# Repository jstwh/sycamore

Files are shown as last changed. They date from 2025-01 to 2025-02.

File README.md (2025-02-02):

# Sycamore

A python framework for Quad-EX.

### Contribution Guidelines

Branch names should state your name and purpose: e.g. joost/walking-engine

All files are formatted with the ruff formatter. Usage: ruff format

Make a branch, don't commit directly to main. If you want to, fork the repo.

### Setup

Create a venv, and install the dependencies as specified in `requirements.txt`:

```sh
python -m venv .venv
source .venv/bin/activate
pip install -r requirements.txt
```

### Setting Up Permissions

Run the following script to set up the necessary permissions for accessing input devices (controller):

```bash
./setup.sh
```

### Linux Service

There is a linux service that runs on startup, it is necessary to display the raspberry pi ip on the lcd, it executes: "python main.py --motors", so it does not turn on motors. The contents of the linux service file can be found in the sycamore.service file in the linux folder. The actual file is present on the raspberry pi under:

```
/etc/systemd/system/sycamore.service
```

some commands for usage:

```
sudo systemctl daemon-reload
sudo systemctl restart sycamore.service
sudo systemctl status sycamore.service

# Uses killsignal SIGINT which works like a keyboard interrupt
sudo systemctl stop sycamore.service
```

If the program fails (for example the ip doesn’t show up) the error gets redirected and can be seen with the command:

```
journalctl -u sycamore.service -f
```

### Arduino

The files for arduino can be found under the arduino map. The file "main.ino" is currently on the arduino and handles showing the ip and streaming data from the ultrasonic distance sensors from the arduino to the raspberry pi.

There is also an "imu.ino" file which was used to test the imu but is not integrated yet. It is up to future collaborators to properly integrate the imu. Note that the imu is currently also not properly placed within Quad-EX, this should also be done for it to work as intended.

For further information about the IMU, see [https://learn.adafruit.com/adafruit-bno055-absolute-orientation-sensor/arduino-code]().

### Argparse

Argparse is an argument parser for python and is used within sycamore to enable or disable certain features on execution. Note that the values are boolean and that the action thus determines the default and what it does. For example:

```
parser.add_argument(
        "--arduino",
        action="store_false",
    )
```

store_false means that the default is True and that you can disable arduino by adding a --arduino flag. Please DO NOT do --arduino False, this is not necessary and will not work.

### Walking Engine

The walking engine is based on various papers, codebases and our own tinkering. Some useful links are:

[https://www.researchgate.net/publication/332374021_Leg_Trajectory_Planning_for_Quadruped_Robots_with_High-Speed_Trot_Gait]()

[https://spotmicroai.readthedocs.io/en/latest/kinematic/#setup-our-3d-ouput]()

[https://www.researchgate.net/publication/322594373_Inverse_Kinematic_Analysis_of_a_Quadruped_Robot]()

[https://github.com/miguelasd688/4-legged-robot-model]()

For documentation about how the walking engine works please contact Makerspace staff and ask for the final report from Quad-EX.

Some important notes are:

The coordinate frame for the foot matrix is:

```
        """
        -x
            |
            |
            |    /  z
            |   /
            |  /
            | /
            |/____________  -y
        """
```

The inverse kinematics, providing the joint angles for the servo's, are calculated in ik.py. These joint angles are then given by providing the LegPoints matrix, containing the end effectors of all four feet, into the JointAngleProvider. The joint angle provider will then provide the angles which can be passed on into the ServoFactory class which will move the actuators. Note that the actuators have a calibration that makes them work, this is why there are servo_flip and servo_map methods in ServoFactory.

### Manual Servo Calibration

The servo's are manually calibrated. This is based on how the legs should move. This entire process is done manually and we never made a consice calibration method. This, again, is something a new contributor might work on. The test_servos.py file is available for some testing when you're calibrating.

### Visualizations

In order to visualize the robot we use rerun. It is a state of the art robotics visualization program and we highly recommend looking it up and reading through the documentation before use. When you want to visualize something you should add the ipv4 from your laptop into rr.connect_tcp("[your laptop ip]:9876"). Note that you should have a rerun window open when you run this, it won't open a window by itself. There is a visualization.py file, most of it is outdated but we kept it in since it might give new contributors some idea of how to visualize something.

### Controller

The controller is something we worked on but it is not properly integrated into the framework, see margriet/controller-input. We recommend going for the evdev approach over the pygame approach for lower overhead and utilizing the controller for simple things should not require much effort besides what we have already implemented.

### Sensors

The sensors that we properly wrote code for are the distance sensors and the lcd. There are also two camera's. We have conducted tests with camera's in an isolated environment but they are not integrated into the framework yet. It might be worthwhile for a new contributor to work on this.

### Mechanical

See [here](build_instructions/README.md).

### Electronics

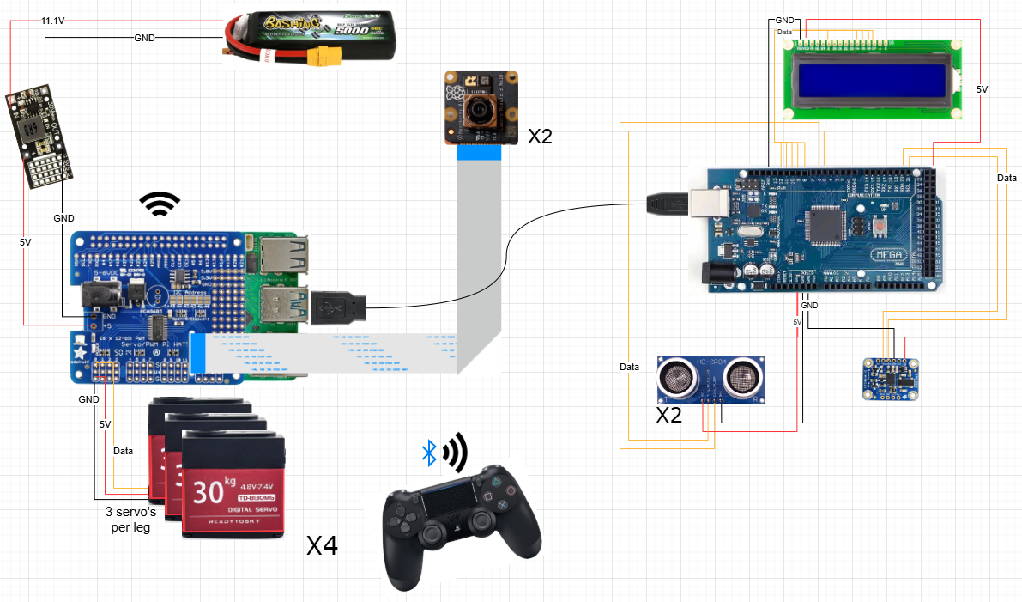
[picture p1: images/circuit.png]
Circuit


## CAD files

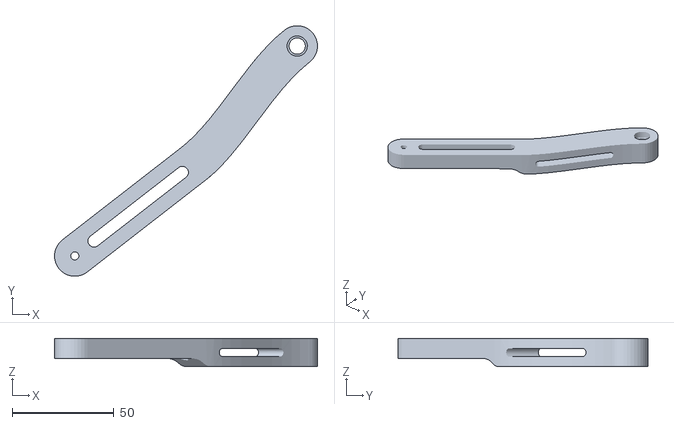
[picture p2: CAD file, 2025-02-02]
build_instructions/stl_files/Body_assemb - Leg_assembly_top_left-1 tibia_mirrored-1.STL
129.4 x 123.3 x 14.0

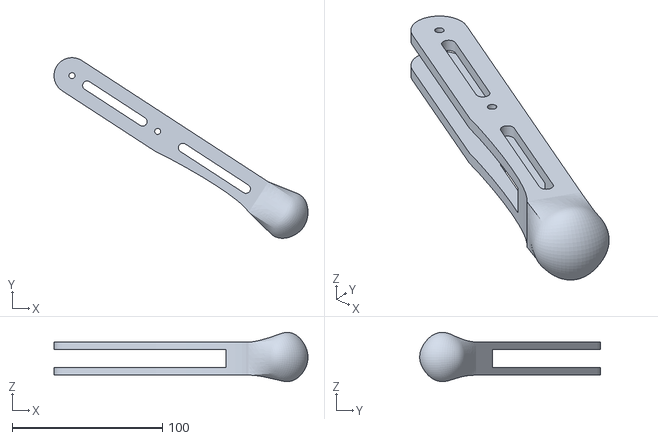
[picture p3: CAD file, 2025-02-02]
build_instructions/stl_files/Body_assemb - Leg_assembly_top_left-1 foot 1.2-1.STL
168.9 x 120.2 x 32.7

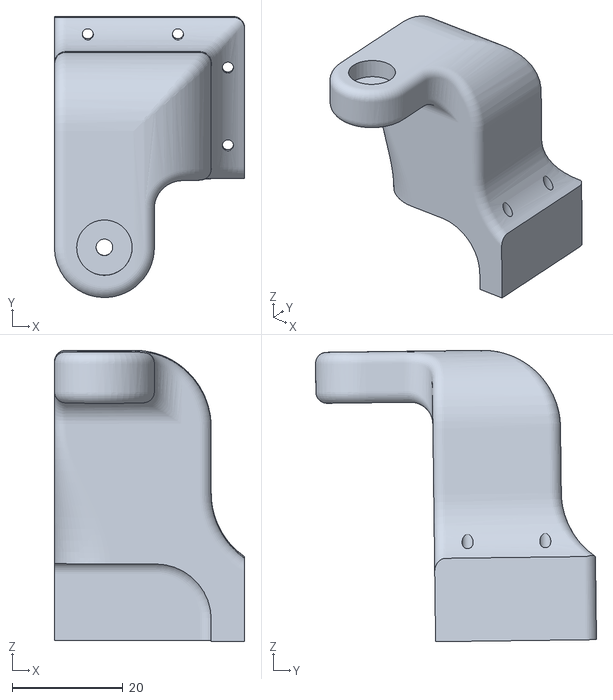
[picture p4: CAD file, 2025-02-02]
build_instructions/stl_files/Body_assemb - Leg_assembly_top_right-1 Hip holder1.2-4.STL
34.2 x 50.6 x 52.5

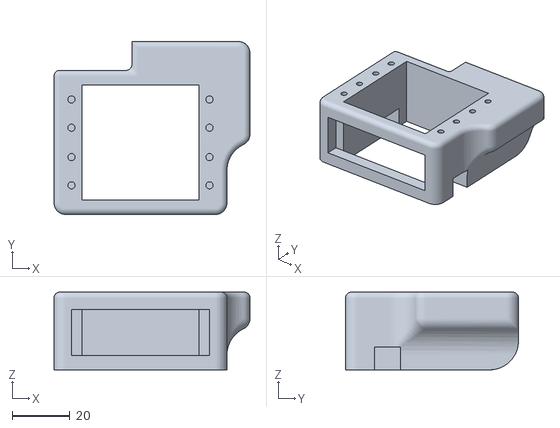
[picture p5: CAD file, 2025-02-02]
build_instructions/stl_files/Body_assemb - Leg_assembly_bottom_right-1 servo_housing-1.STL
68.0 x 60.0 x 27.0

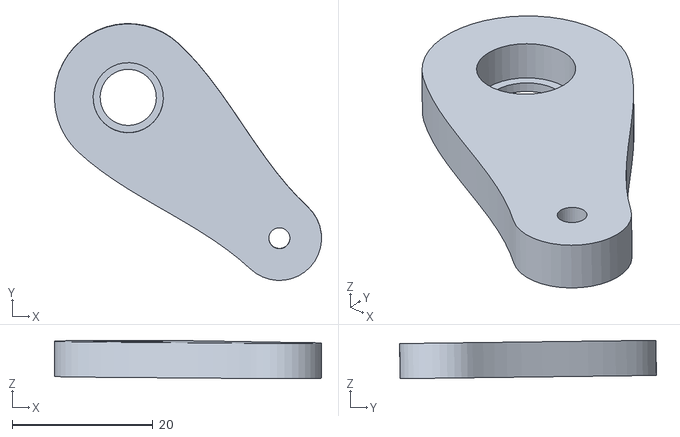
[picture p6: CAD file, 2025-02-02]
build_instructions/stl_files/Body_assemb - Leg_assembly_top_right-1 small link 1.2-2.STL
38.0 x 36.5 x 5.46

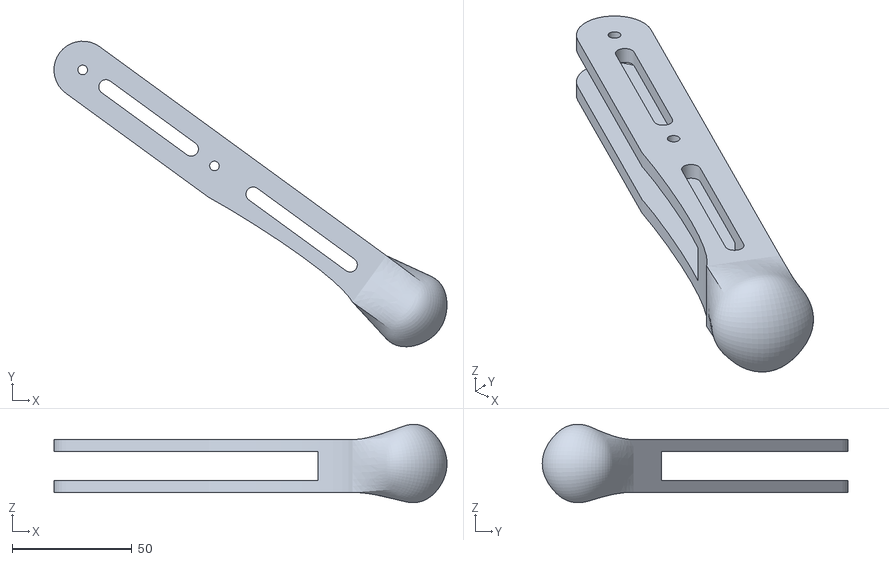
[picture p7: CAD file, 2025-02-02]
build_instructions/stl_files/Body_assemb - Leg_assembly_bottom_right-1 foot 1.2-4.STL
163.9 x 127.4 x 32.7

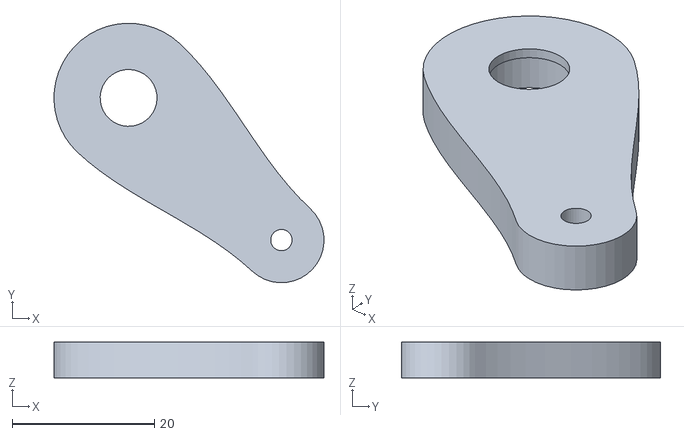
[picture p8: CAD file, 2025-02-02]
build_instructions/stl_files/Body_assemb - Leg_assembly_top_left-1 small link1.2-1.STL
38.0 x 36.5 x 5.00

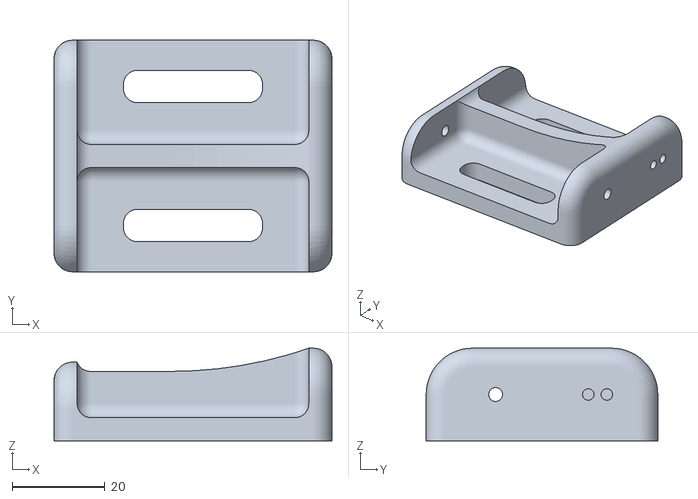
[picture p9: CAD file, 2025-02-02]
build_instructions/stl_files/Body_assemb - leg_assembly_bottom_left-2 extension_servo_housing_v2-1.STL
60.0 x 50.0 x 20.0

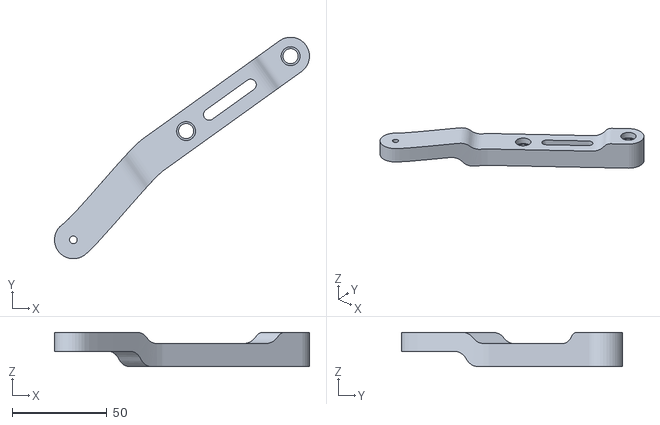
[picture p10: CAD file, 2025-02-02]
build_instructions/stl_files/Body_assemb - leg_assembly_bottom_left-2 fibula_mirrored-1.STL
134.9 x 117.1 x 18.0

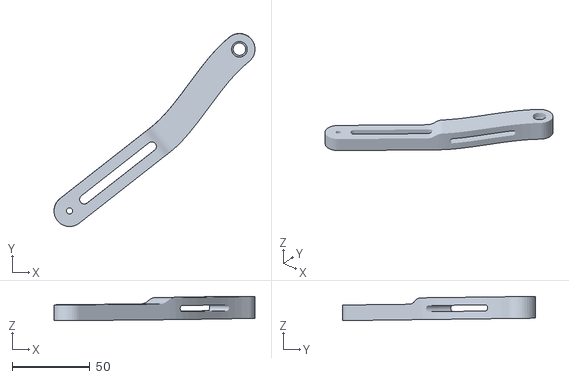
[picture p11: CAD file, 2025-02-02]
build_instructions/stl_files/Body_assemb - Leg_assembly_top_right-1 tibia_scaled 1.2-3.STL
129.0 x 123.9 x 15.6

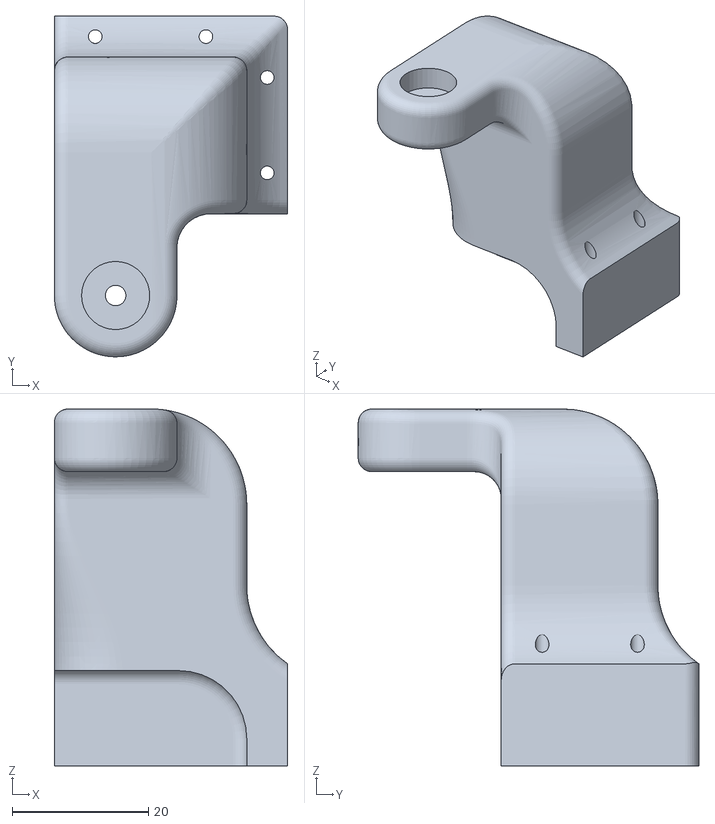
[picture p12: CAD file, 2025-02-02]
build_instructions/stl_files/Body_assemb - Leg_assembly_bottom_right-1 Hip Holder 1.2-4.STL
34.2 x 50.0 x 52.4

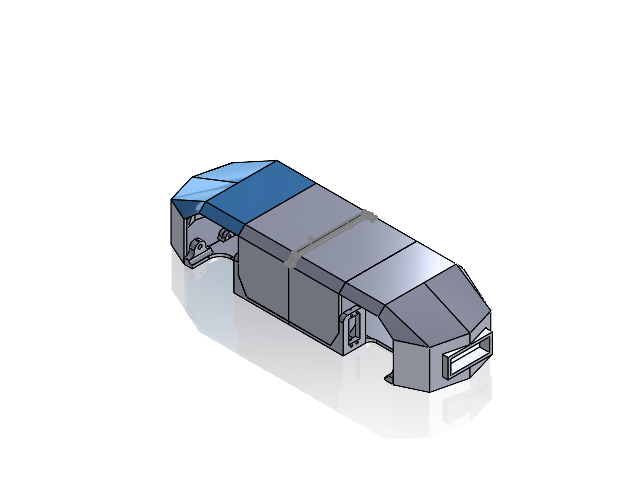
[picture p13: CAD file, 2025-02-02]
build_instructions/Solidworks Files/.OPEN HERE_Body Assembly SMALL.SLDASM
Body Skeleton front panel SMALL x 2
Front panel SMALL
middle panel SMALL x 2
front panel top SMALL x 2
back panel updated SMALL

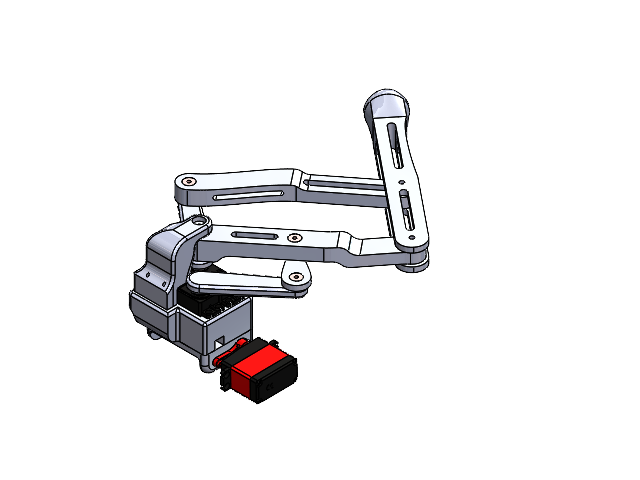
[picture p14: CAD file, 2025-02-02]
build_instructions/solidworks/Leg_assembly_top_right.SLDASM
servo_housing
CAD_TD-8120mg_Tiankongrc_DigitalServo x 3
SERVO ARM HORN 25T ALUMINIUM x 3
M2 CAP HEAD SOCKET SCREW x 6
servo_horn_extension_mock x 2
small thing 1.2
Bearing x 8
Large_linkage_1.2
fibula_scaled 1.2
tibia_and_foot 1.2
extension_servo_housing_v2
Hip Joint 1.2

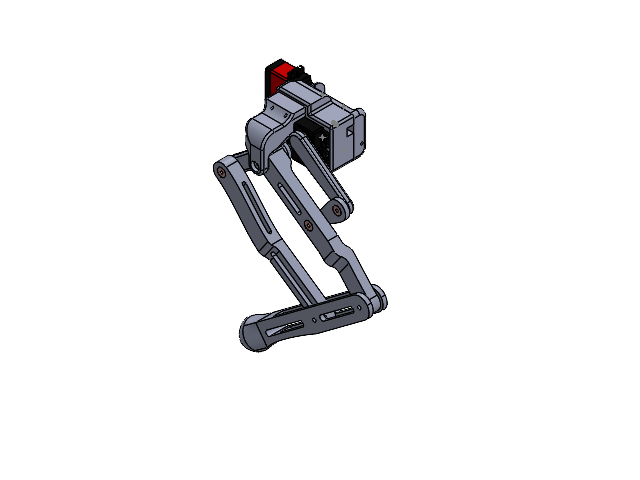
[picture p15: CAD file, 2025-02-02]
build_instructions/solidworks/leg_assembly_bottom_left.SLDASM
CAD_TD-8120mg_Tiankongrc_DigitalServo x 3
SERVO ARM HORN 25T ALUMINIUM x 3
M2 CAP HEAD SOCKET SCREW x 6
servo_horn_extension_mock x 2
mirrored_servo_housing
small thing 1.2
Bearing x 7
large_linkage_mirrored
fibula_mirrored
tibia_and_foot 1.2
mirrored_hip joint
extension_servo_housing_v2

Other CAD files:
build_instructions/stl_files/Body_assemb - leg_assembly_bottom_left-2 tibia_mirrored-1.STL
build_instructions/stl_files/Body_assemb - Leg_assembly_bottom_right-1 small link 1.2-2.STL
build_instructions/stl_files/Body_assemb - leg_assembly_bottom_left-2 mirrored_hip holder-1.STL
build_instructions/solidworks/Bearing.SLDPRT
build_instructions/solidworks/Body Skeleton Bottom_front panel.SLDPRT
build_instructions/solidworks/Front panel.SLDPRT
build_instructions/solidworks/Hip Joint 1.2.SLDPRT
build_instructions/solidworks/Large_linkage_1.2.SLDPRT
build_instructions/solidworks/Leg_assembly_bottom_right.SLDASM
build_instructions/solidworks/Leg_assembly_top_left.SLDASM
build_instructions/solidworks/M2 CAP HEAD SOCKET SCREW.SLDPRT
build_instructions/solidworks/Mirrored Body Skeleton Bottom back.SLDPRT
build_instructions/solidworks/SERVO ARM HORN 25T ALUMINIUM.SLDPRT
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

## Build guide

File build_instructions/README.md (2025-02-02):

# Build Instructions For Quad-EX

### Leg Assembly

Below you can find a general assembly of the leg, with each part labelled exactly as the STL file. (this particular assembly is the top left leg).

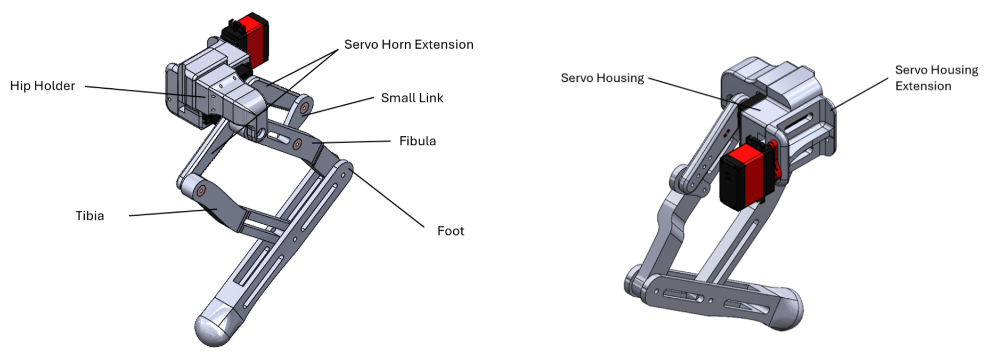
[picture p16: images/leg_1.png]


The first step is to assemble the servos with their servo horns and associated servo extension. The exploded view below shows this visually.

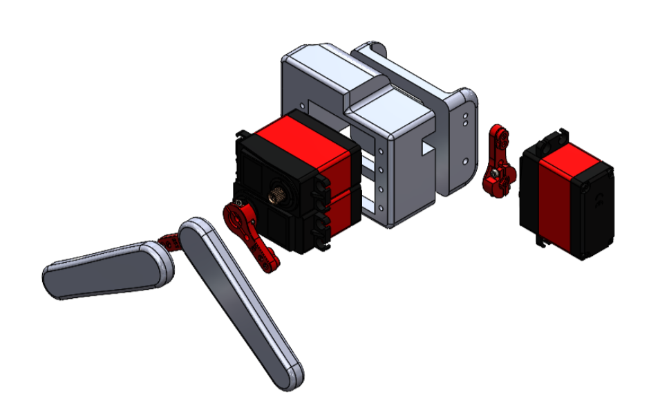
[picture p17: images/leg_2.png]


**Important:** The servo horn must be tightened on the servo using the small screws it comes with. Otherwise, the horn doesn’t stay on.

**Important:** The servo housing barely fits the servos (design mistake). This means you will have to push the servos in quite hard, and that the cables won’t go through. Therefore, you will have to unscrew the servo from the back to move the cable out of the way, place it in the housing and then screw it back on once it is fitted in. The advantage is that you won’t have to make use of the holes that are on the servo housing; the servos stay attached.

**Important:** To connect the servo housing extension to the servo housing, you will have to use screws. This is an annoying procedure, and an obvious design flaw. I recommend using only two screws placed diagonally away from each other. Tip: Make a small hole using a drill, then use a screwdriver to fit in the screw. You can also use hot glue to temporarily secure the servo housing extension, so it doesn’t move around when you use the screw driver. A clamping mechanism can also work.

**Important:** The servo horn extension needs to be securely attached to the servo horn. I recommend using a short bolt. For the servo that has the hip holder, do not use a bolt now, since you will block the way. Instead, bolt it in the next available hole. For the other servo, it doesn’t matter.

At this stage, the assembly should look like this:

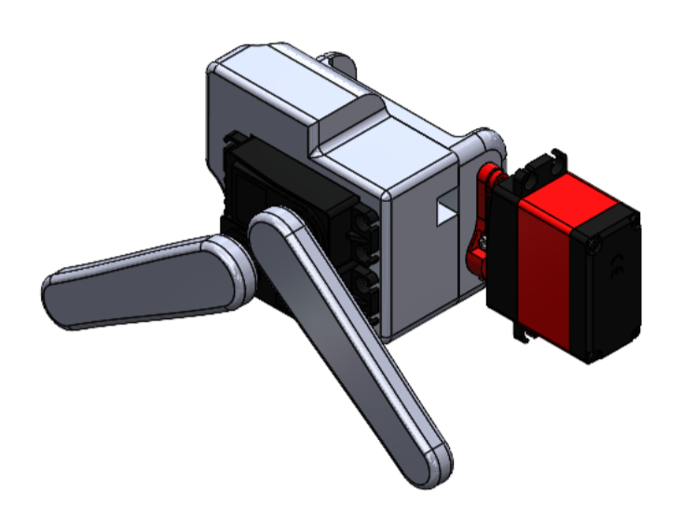
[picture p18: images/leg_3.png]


The next step is to add all the bearings into the tibia, fibula and small link. The bearings needed are sized 10 mm x 3 mm with 4 mm thickness. The link to the exact bearing used for this project is found here: [https://www.123-3d.nl/123-3D-Kogellager-623ZZ-1-stuk-i18-t13131.html](https://www.123-3d.nl/123-3D-Kogellager-623ZZ-1-stuk-i18-t13131.html).

Once the bearings are pressed into the design (you may need to use a hammer), you can begin to assemble them into the leg. To join all the parts together, you will have to use M3 bolts as the axles for the bearings. The exact length of the bolt use doesn’t matter, but try to give enough room for at least 2 nuts to be used to tighten the parts together. Below is an exploded view of how to assemble it all:

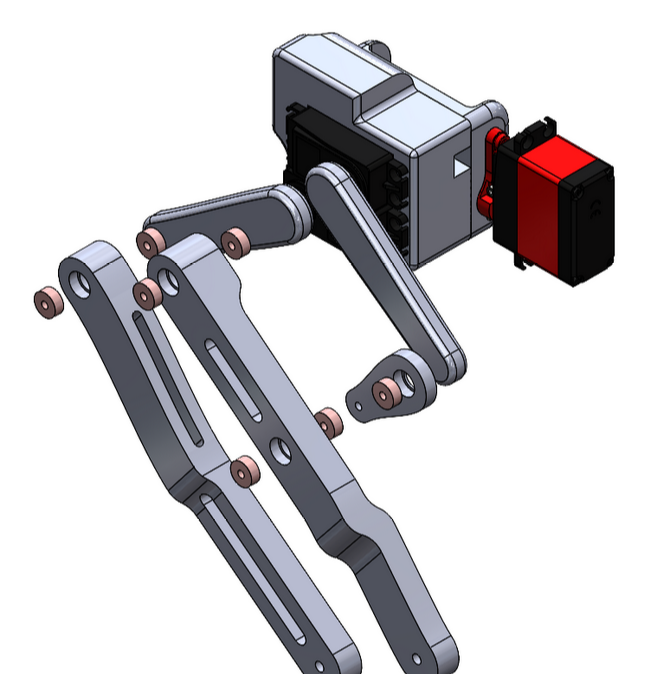
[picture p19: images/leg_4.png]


Important: when assembling the bearings, its ok to use a hammer as long as you use some protective layer in between (a piece of cloth). Not doing this will likely damage the bearing.![A grey robot with black and red camera

Description automatically generated](https://lh7-rt.googleusercontent.com/docsz/AD_4nXf04_a5LGCbkeIS03O4nxMCbhMkc0Si71HrTsmSB4adKIBdWNtUNUzPWMYvs5UkJkEeqAskypdqnVYeOHyNs4cIIoge8c2DjL6uu1v-mTolVBD5RWc4NS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)

Important: Don’t tightening the bolts on the bearings too hard, it will “pinch” the bearings which won’t make them work.

Important: Use washers in plastic-plastic interfaces. Not only is this important to reduce friction, but also is important when assembling the foot.

Important: Do not yet use a bolt on the hip joint, since the hip holder still has to be attached.

Tip: I recommend using nyloc nuts as they prevent loosening due to vibrations. It makes a really big difference. If you don’t, I suggest using two nuts after each other.

Once this is all assembled, you can begin assembling the foot. This is relatively simple, just use bolts, nuts and washers. The below figure shows the stage you should be at now.

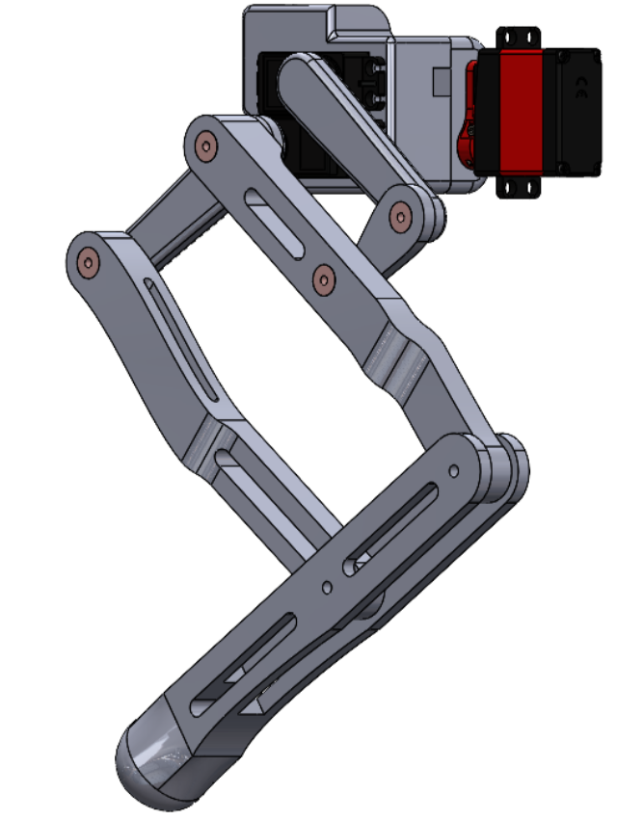
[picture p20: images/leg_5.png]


You can now add the hip holder to the leg assembly. You will need one bearing, and a rather long, 40mm M3 bolt to hold all the parts attached to the hip.

**Important:** To attach the hip holder on the servo housing, screws were used. This turned out rather bad for us, so I recommend using PLA glue instead.

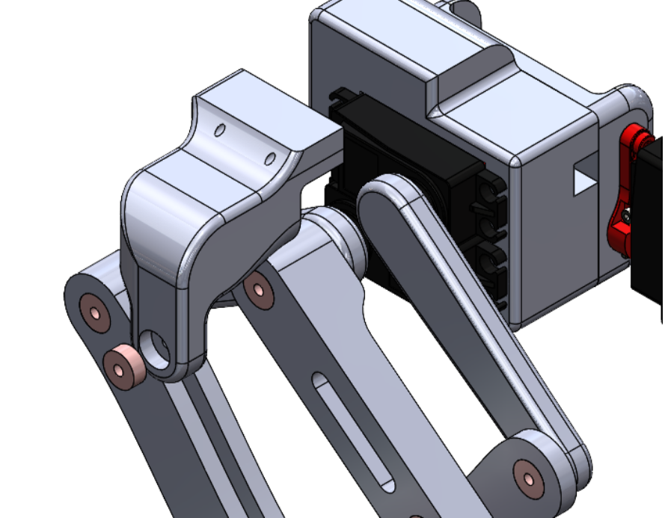
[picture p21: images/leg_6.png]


The leg is now assembled.

### Body Assembly

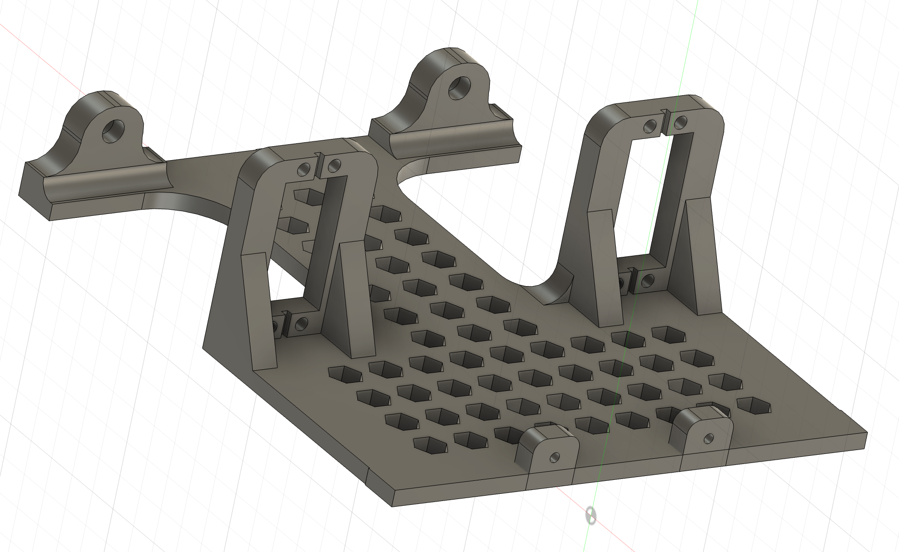
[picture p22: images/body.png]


This is half of the robot's body, 3D printed as part of a two-piece assembly. Two parts can be connected using screws and nuts through the smaller supports at the ends. These smaller supports provide a secure fit for the assembly. Inside the larger supports, each is fitted with a bearing, allowing a screw to pass through the bearing and secure the leg to the body. The hip servo motor is housed in the support with a rectangular opening. Once in place, the servo motor can be attached to the leg as described in the leg assembly section above, ensuring a smooth and stable connection for the robot's movement.

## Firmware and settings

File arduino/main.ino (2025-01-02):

#include <LiquidCrystal.h>

LiquidCrystal lcd(7, 8, 9, 10, 11, 12);

const int trigger_pin_left = 3;
const int echo_pin_left = 2;
const int trigger_pin_right = 5;
const int echo_pin_right = 4;

float speed_of_sound = 343.2611; //Meters per second at 20C (ADJUST FOR DIFF TEMPS!)
float conversion_factor = .0001;
unsigned int ping_time = 0;

bool ip_displayed = false;
String ip_address = "";

void setup() {
  pinMode(trigger_pin_left, OUTPUT);
  pinMode(echo_pin_left, INPUT);
  pinMode(trigger_pin_right, OUTPUT);
  pinMode(echo_pin_right, INPUT);
  Serial.begin(9600);
  lcd.begin(16, 2);
  lcd.print("Waiting for IP");
}

float distance(int triggerPin, int echoPin) {
  /* distance returns a float value in centimeters */
  float dist = 0.0;

  digitalWrite(triggerPin, LOW);
  delayMicroseconds(5);
  digitalWrite(triggerPin, HIGH);
  delayMicroseconds(12);
  digitalWrite(triggerPin, LOW);
  ping_time = pulseIn(echoPin, HIGH, 18000);

  if (ping_time == 0) {
    return -1; // Return -1 if no valid echo received
  }

  dist = speed_of_sound * conversion_factor * ping_time / 2;
  return dist;
}

void loop() {
  // Handle IP Address Display
  if (Serial.available() > 0 && !ip_displayed) {
    ip_address = Serial.readStringUntil('\n');
    lcd.clear();
    lcd.print(ip_address);
    ip_displayed = true;
  }

  // Handle Distance Measurement
  if (ip_displayed) {
    float answer_left = distance(trigger_pin_left, echo_pin_left);
    float answer_right = distance(trigger_pin_right, echo_pin_right);

    Serial.println(String(answer_left) + "," + String(answer_right));

    delay(200);
  }
}

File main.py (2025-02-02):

import time
import numpy as np
import rerun as rr
from motion.walking_engine import WalkingEngine
import argparse
import serial
from sensors.lcd import display_ip
from sensors.distance import DistanceReader
from motion.ps4 import Controller


PORT = "/dev/ttyACM0"
BAUDRATE = 9600


def init_rerun():
    rr.init("Quad-EX visualization")
    rr.connect_tcp("127.0.0.1:9876")


def parse_args():
    parser = argparse.ArgumentParser(description="Quad-EX CLI")

    parser.add_argument(
        "--rerun",
        action="store_true",
        help="Flag for enabling rerun. Default set to False.",
    )

    parser.add_argument(
        "--controller",
        action="store_true",
        help="Flag that can be enabled if you want to control the robot with a PS4 controller.",
    )

    parser.add_argument(
        "--motors",
        action="store_false",
        help="Flag that can be turned off if you do not want to use the servo hat. Default is True.",
    )

    parser.add_argument(
        "--arduino",
        action="store_false",
        help="Flag that can be disabled if not using an arduino. Default is True.",
    )

    return parser.parse_args()


def main_control_loop(we, distance_reader, args):
    interval = 0.030
    startTime = time.time()
    lastTime = startTime

    while True:
        if time.time() - lastTime >= interval:
            loopTime = time.time() - lastTime
            lastTime = time.time()
            t = time.time() - startTime

            if args.controller:
                controller = Controller()
                v, angle, w_rot = controller.read()
                we.walk_with_controller(v, angle, w_rot)

            else:
                # Give the arduino time to send over serial
                if args.arduino and distance_reader.left:
                    left = distance_reader.left
                    right = distance_reader.right

                    if left < 30 and right < 30:
                        we.walk(direction="left")
                    elif left < 30 and right > 30:
                        we.walk(direction="left")
                    elif left > 30 and right < 30:
                        we.walk(direction="right")
                    else:
                        we.walk(direction="forward")
                else:
                    we.walk(direction="forward")


if __name__ == "__main__":
    args = parse_args()
    print(args.arduino)

    if args.arduino:
        ser = serial.Serial(PORT, BAUDRATE, timeout=0.5)
        display_ip(ser)

    if args.rerun:
        init_rerun()

    l1 = 56
    l2 = 0
    l3 = 150
    l4 = 175
    length = 265
    width = 110
    """
      -x
        |
        |
        |    /  z
        |   /
        |  /
        | /
        |/____________  -y
    """
    LegPoints = np.array(
        [
            [180, -220, 130, 1],  # LF
            [180, -220, -130, 1],  # RF
            [-20, -190, 130, 1],  # LB
            [-20, -190, -130, 1],  # RB
        ]
    )

    we = WalkingEngine(l1, l2, l3, l4, length, width, LegPoints, args)
    we.reset_body()
    we.init_walk()

    if args.arduino:
        ser = serial.Serial(PORT, BAUDRATE, timeout=0.5)
        distance_reader = DistanceReader(ser)
        distance_reader.start()

        try:
            main_control_loop(we, distance_reader, args)
        except KeyboardInterrupt:
            distance_reader.stop()
            distance_reader.join()
            ser.close()
    else:
        main_control_loop(we, None, args)

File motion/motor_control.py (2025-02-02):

from adafruit_servokit import ServoKit
from math import degrees


class ServoFactory:
    def __init__(self):
        self.kit0 = ServoKit(channels=16, address=0x42)
        self.kit1 = ServoKit(channels=16, address=0x44)
        # Left Front, in order: theta1, theta2, theta3
        self.kit0.servo[0].set_pulse_width_range(500, 2500)
        self.kit0.servo[1].set_pulse_width_range(500, 2500)
        self.kit0.servo[2].set_pulse_width_range(500, 2500)
        # Left Back, in order: theta1, theta2, theta3
        self.kit0.servo[3].set_pulse_width_range(500, 2500)
        self.kit0.servo[4].set_pulse_width_range(500, 2500)
        self.kit0.servo[5].set_pulse_width_range(500, 2500)
        # Right Front, in order: theta1, theta2, theta3
        self.kit1.servo[6].set_pulse_width_range(500, 2500)
        self.kit1.servo[7].set_pulse_width_range(500, 2500)
        self.kit1.servo[8].set_pulse_width_range(500, 2500)
        # Right Back, in order: theta1, theta2, theta3
        self.kit1.servo[9].set_pulse_width_range(500, 2500)
        self.kit1.servo[10].set_pulse_width_range(500, 2500)
        self.kit1.servo[11].set_pulse_width_range(500, 2500)

    def move_servos(self, lf: tuple, lb: tuple, rf: tuple, rb: tuple):
        """
        Provided a tuple containing (theta1, theta2, theta3) from the inverse kinematics for each
        leg, move the servos.

        There is an offset for each servo, this is based on the fact that the zero position of the
        servo is different from the zero position of the actual leg attached. This offset occurs
        because the little metal gear that you attach the servo arm to will force you to have an
        offset in the arm which causes it to be close but not perfectly equal to the position. If
        the legs get de-assembled or changed this will have to be done manually again to figure out
        the new offsets.
        """
        Lf = to_deg(lf)
        Lb = to_deg(lb)
        Rf = to_deg(rf)
        Rb = to_deg(rb)
        # LF
        self.kit0.servo[0].angle = servo_mapping(Lf[0]) + 25
        self.kit0.servo[1].angle = servo_flip(servo_mapping(Lf[1]) - 15)
        self.kit0.servo[2].angle = Lf[2] + 20
        # LB
        self.kit0.servo[3].angle = servo_flip(servo_mapping(Lb[0]) - 15)
        self.kit0.servo[4].angle = servo_flip(servo_mapping(Lb[1]) - 16)
        self.kit0.servo[5].angle = Lb[2] + 8
        # RF
        self.kit1.servo[6].angle = servo_flip(servo_mapping(Rf[0]) - 15)
        self.kit1.servo[7].angle = servo_mapping(Rf[1] - 5)
        self.kit1.servo[8].angle = servo_flip(Rf[2] - 10)
        # RB
        self.kit1.servo[9].angle = servo_mapping(Rb[0]) + 4
        self.kit1.servo[10].angle = servo_mapping(Rb[1]) + 10
        self.kit1.servo[11].angle = servo_flip(Rb[2]) + 5


def to_deg(leg_angles):
    """
    Change the output from leg IK from radians to degrees.
    """
    return (degrees(leg_angles[0]), degrees(leg_angles[1]), degrees(leg_angles[2]))


def servo_flip(angle):
    """
    Flips the direction that the servo moves in.
    """
    return 180 - angle


def servo_mapping(angle):
    """
    Maps the output from the leg IK to an input usable by the 180degree servo's.
    -90 to 90 -> 0 to 180
    """
    return angle + 90

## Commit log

2024-11-23 Added servo support in control
2024-12-08 practice with leg control
2024-12-12 tooling for manual servo calibration
2024-12-20 body assembly calibration
2024-12-30 introduce distance sensors and lcd screen
2024-12-30 add arduino flag and functionality
2025-01-02 update servo testing
2025-01-02 hotfix threading
2025-01-04 maybe fix ip display
    [main.py]
2025-01-14 added additional arduino support
2025-01-14 leg kinda works
2025-01-15 try out new calibration
2025-01-17 Hotfix for args not working properly
    [main.py, utils.py]
2025-01-20 calibrating updated
2025-02-02 add stl and solidworks files
    [.OPEN HERE_Body Assembly SMALL.SLDASM, Bearing.SLDPRT, Body Assemb SMALL - Body Skeleton front panel SMALL-1.STL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]
2025-02-02 naming conventions
    [.OPEN HERE_Body Assembly SMALL.SLDASM, Bearing.SLDPRT, Body Assemb SMALL - Body Skeleton front panel SMALL-1.STL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]
2025-02-02 more naming
    [.OPEN HERE_Body Assembly SMALL.SLDASM, Body Assemb SMALL - Body Skeleton front panel SMALL-1.STL, Body Assemb SMALL - Body Skeleton front panel SMALL-2.STL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]
